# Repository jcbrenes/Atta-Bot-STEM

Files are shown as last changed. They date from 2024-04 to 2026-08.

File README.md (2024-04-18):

# Atta-Bot-STEM

Proyecto de investigación Atta-Bot STEM del Tecnológico de Costa Rica (código VIE 5402-1440-5101), con participación de la Escuela de Matemática y la Escuela de Ingeniería Mecatrónica. 

## Objetivo 
Diseñar y desarrollar una plataforma robótica de bajo costo, compuesta por un robot educativo acompañado de una aplicación computacional interactiva y amigable, guías de trabajo llamadas unidades didácticas y manuales de usuario, con el propósito de fomentar y fortalecer la enseñanza de las ciencias, tecnología, ingeniería y matemáticas (STEM) en estudiantes de Educación General Básica (EGB).

## Período de ejecución
Enero 2024 - Diciembre 2026

## Equipo investigador
- **Cindy Calderón Arce.** ORCID: https://orcid.org/0000-0002-0077-225X  
- **Rebeca Solís Ortega.** ORCID: https://orcid.org/0000-0002-3065-8386  
- **Juan Carlos Brenes Torres.** ORCID: https://orcid.org/0000-0001-6323-2173  
- **Dylana Freer Paniagua.** ORCID: https://orcid.org/0009-0005-8539-7901  

## Directorio de carpetas
- App -> Directorio con el código fuente para la aplicación de programación del robot
- Robot -> Proyecto en Arduino IDE para la programación del controlador del robot
- Chasis -> Diagramas y archivos para el chasís y parte mecánica del robot
- Materiales -> Lista de materiales usados en la construcción del robot
- Docs -> Documentos que describen el armado, programación, y uso del robot.
- Publicaciones -> Datos y materiales referentes a publicaciones del proyecto en revistas científicas.  

## Estándar de programación
Para contribuciones al proyecto se debe seguir el estándard de código o programación detallado en el archivo [Contributing.md]

[Contributing.md]: <https://github.com/jcbrenes/Atta-Bot-STEM/blob/main/CONTRIBUTING.MD>

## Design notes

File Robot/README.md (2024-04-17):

# Directorio Robot 

 Código para la programación del controlador del robot

 Lenguaje: C++
 Ambiente de programación: Arduino IDE
 Microncontrolador usado: IdeaBoard (basada en ESP32)

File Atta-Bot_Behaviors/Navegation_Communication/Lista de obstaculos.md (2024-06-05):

# Lista de mensajes

Distribución de los mensajes:
- Los mensajes se componen de 7 valores separados por ";" y el orden de lectura es:
	- ID: número de identificación del robot
	- Coordenada X
	- Coordenada Y
	- Orientación
	- Tipo de mensaje
	- Distancia a obstaculo: para sensor sharp
	- Ángulo de obstaculo: para sensor sharp

El tipo de mensaje indica a que se refiere el resto de la información en el mensaje.

Lista de tipos de mensajes que se van a recibir en la base:
- 0: Identifica posición sin obstaculo
- 1: Sharp, da medida de distancia y ángulo
- 2: IR frontal
- 3: IR derecho
- 4: IR izquierdo
- 5: Temperatura
- 6: Batería baja 
- 15: El Atta completó la función avanzarCoordenada y deja de avanzar
- 20: Medición de distancia inicial para coordinación de coordenadas
- 40: Falla de magnetómetro
- 41: Falla de MPU

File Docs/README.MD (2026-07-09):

# Documentación proyecto Atta-Bot STEM

Documentación que describe la arquitectura, protocolos, uso y programación del robot y la aplicación

ATTABUGS: https://estudianteccr-my.sharepoint.com/:x:/g/personal/prof\_ccalderon\_estudiantec\_cr/IQCo-vc9WYxwTrwLP-bhTWXTAcZCWMQx9sQ\_CMA\_rZHOI40?rtime=Aeg34Gbd3kg

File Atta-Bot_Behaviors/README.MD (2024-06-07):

**Atta-Bots: Adaptaciones, comportamientos y funcionalidades en el marco de los proyectos PROE**

Proyecto de investigación Atta-Bots del Tecnológico de Costa Rica (código VIE 5402-1440-5101), con participación de la Escuela de Matemática y la Escuela de Ingeniería Mecatrónica.

Objetivo:
Diseñar nuevos comportamientos y funcionalidades en los Atta-Bots construidos en PROE: E1F2 para disminuir la incertidumbre entre lo simulado y lo real.

Período de ejecución:
Enero 2022 - Diciembre 2023

Equipo investigador:

Cindy Calderón Arce. ORCID: https://orcid.org/0000-0002-0077-225X

Rebeca Solís Ortega. ORCID: https://orcid.org/0000-0002-3065-8386

Juan Carlos Brenes Torres. ORCID: https://orcid.org/0000-0001-6323-2173

Repositorio de: 

Código computacional de comunicación entre robots.

Código computacional de mapeo en tiempo real.

Código computacional de generación de rutas óptimas en tiempo real.

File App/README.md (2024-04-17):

# Directorio App
Código para la aplicación de programación del robot.

Lenguaje: 
Ambiente de programación:
Requerimientos:

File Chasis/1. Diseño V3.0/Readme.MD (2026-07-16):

El archivo de ensamble del Robot AttaBot completo se llama "Ensamble\_completo.iam".

Este ha sido trabajado por última vez en Inventor 2027.

Cabe destacar que existe una pieza tipo iPart que es la base del chasis. Esta contiene una tabla de parámetros para los cotas de la pieza realizado por el antiguo asistente llamado Carlos Arguello (un grande).

Sin embargo la piezas piezas "Bumper Trasero" y "Esquinero Trasero" fueron creadas a partir de esta pieza mencionada, por lo cuál inventor genera una carpeta automáticamente de cada pieza para mantener la tabla de componentes original. Es por esta razón que aislamos estas carpetas en la llamada "iParts". Por favor NO eliminar esta carpeta porque generaría problemas de reconstrucción del ensamble.

La carpeta de Set de Herramientas son todos los archivos referentes al TFG del estudiante Jose Carlos. En en ensamble Completo ya se encuentra el ensamble de Jose Carlos del Set de Herramientas incluido. Si que quisiera suprimir use como guia la imagen "GuiaParaQuitarElSetDeHerrmientasDentroDelEnsamble.png", esto sería seleccionando las carpetas del ensamble que interesan y usando la operación ISOLATE. 

La carpeta Content Center Files contiene toda la tornillería del ensamble para no depender de si el usuario tiene el instalado la carpeta de Toolbox o no. De momento hacen falta alguna que otra tuerca o tornillo en el ensamble, pero de poca relevancia para el estado actual del proyecto.

La Carpeta de "Molde para Curva Trasera" contiene todo el trabajo en inventor realizado para el molde de la curva por si quisiera rediseñar el mismo. Sin embargo el archivo pdf listo para mandar a cortar otro molde se encuentra en la carpeta de "Archivos para impresión".

Las carpetas de "OldVersions" que aparecen por todo lado son creadas automáticamente por Inventor cuando se actualizan archivos. Estarlas limpiando continuamente es una buena práctica para no llenar el git de basura, ya que el control de versiones se maneja con los commits directamente.

Redactado el 13/07/2026 por el asistente Aarón Valerín Páez (aavalerin@estudiantec.cr)

&#x20;

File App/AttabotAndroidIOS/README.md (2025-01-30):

# Atta-Bot Educativo
El proyecto Attabot Educativo es un proyecto de código abierto que busca fomentar la educación en la programación y robótica en niños y jóvenes de una manera divertida y sencilla.

**Dentro de este proyecto se encuentra el código fuente de la aplicación móvil que se conecta con el robot Attabot**

## Requisitos
- Android Studio
- Dispositivo Android con versión 5.0 o superior
- Flutter SDK
- (Opcional) Extensiones de VSCode para Flutter y Dart

## Instalación
1. Clonar el repositorio
```bash
git clone
```

2. Abrir el proyecto en VSCode 
```bash
cd Atta-Bot-STEM/App/AttabotAndroidIOS
code .
```

3. Ejecutar el proyecto
```bash
flutter run
```

## Estructura del proyecto
El proyecto utiliza una estructura basada en Screaming Architecture y componentes, la cual se divide en tres capas principales:

- **Features**: Contiene las funcionalidades de la aplicación, cada funcionalidad se divide en componentes, enums, models y services.
```
    - feature1
        - components
        - enums
        - models
        - services
    - feature2
        - components
        - enums
        - models
        - services
```

- **Pages**: Contiene las páginas de la aplicación, cada página se divide en un archivo para la página y un archivo para cada componente de la página. Dentro de cada pagina se importan las funcionalidades necesarias.
```
    - page1
        - home.dart
        - page1.dart
        - page2.dart
```

- **Shared**: Contiene los componentes servicios e interfaces compartidos entre diferentes funcionalidades, como botones, inputs, etc.

```
    - components
        - button.dart
        - input.dart
    - interfaces
        - bluetoothServiceInterface.dart
    - features
        - components
        - enums
        - models
        - services

```

## Contribuir
Para continuar contribuyendo al proyecto es necesario que el codigo este escrito en **INGLES** y seguir los siguientes pasos:

1. Crear una rama con el nombre de la nueva funcionalidad
```bash
git checkout -b feature/nombre-de-la-funcionalidad
```

2. Realizar los cambios necesarios

3. Hacer commit de los cambios con un mensaje descriptivo en ingles utilizando [Conventional Commits](https://www.conventionalcommits.org/en/v1.0.0-beta.4/)
```bash
git add .
git commit -m "feat: nueva funcionalidad" 
```

## Documentacion de referencia
Ya que el tiempo para documentar adecuadamente el proyecto fue limitado se recomienda revisar en profundidad la siguiente documentacion de referencia:

- [Flutter](https://flutter.dev/docs)
- [Dart](https://dart.dev/guides)
- [Provider](https://pub.dev/documentation/provider/latest/)
- [Flutter Blue Plus](https://pub.dev/documentation/flutter_blue_plus/latest/)

> **Nota:** Es posible que la documentacion de alguna de las dependencias no coincida con la version utilizada en este proyecto, para ello se recomienda revisar la documentacion de la version especifica en el archivo `pubspec.yaml`

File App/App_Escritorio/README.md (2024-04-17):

Aplicación de escritorio desactualizada. No cuenta con soporte o actualizaciones.

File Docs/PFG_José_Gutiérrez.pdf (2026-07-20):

Instituto Tecnológico de Costa Rica

Escuela de Ingeniería Mecatrónica

## Diseño de la expansión de la plataforma robótica Atta-Bot STEM

Informe de Proyecto de Graduación para optar por el título de

Ingeniero en Mecatrónica con el grado académico de Licenciatura

José Carlos Gutiérrez Zúñiga

Cartago, 23 de junio de 2026

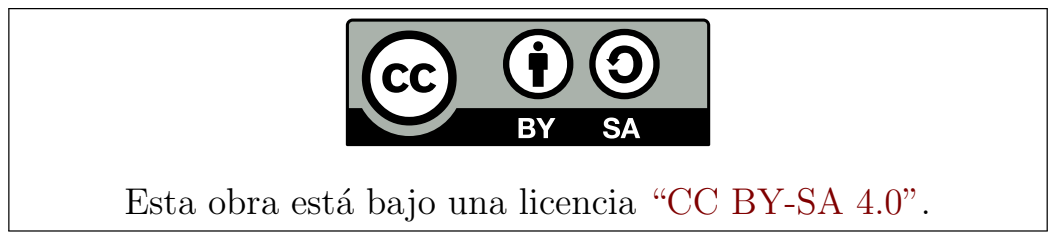
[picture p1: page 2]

Esta obra está bajo una licencia “CC BY-SA 4.0”. (https://creativecommons.org/licenses/by-sa/4.0/deed.en)

Declaro que el presente Proyecto de Graduación ha sido realizado enteramente por mi persona, utilizando y aplicando literatura referente al tema e introduciendo conocimientos propios.

En los casos en que he utilizado bibliografía, he procedido a indicar las fuentes mediante las respectivas citas bibliográficas. En consecuencia, asumo la responsabilidad total por el trabajo de graduación realizado y por el contenido del correspondiente informe final.

José Carlos Gutiérrez Zúñiga

Cartago, 23 de junio de 2026

Céd: 1-1693-0685

### INSTITUTO TECNOLÓGICO DE COSTA RICA PROGRAMA DE LICENCIATURA EN INGENIERÍA MECATRÓNICA PROYECTO FINAL DE GRADUACIÓN ACTA DE APROBACIÓN

El profesor asesor del presente trabajo final de graduación, indica que el documento presentado por el estudiante cumple con las normas establecidas por el programa de Licenciatura en Ingeniería Mecatrónica del Instituto Tecnológico de Costa Rica para ser defendido ante el jurado evaluador, como requisito final para aprobar el curso Proyecto Final de Graduación y optar así por el título de Ingeniero(a) en Mecatrónica, con el grado académico de Licenciatura.

Estudiante: José Carlos Gutiérrez Zúñiga.

Proyecto: Diseño de la expansión de la plataforma robótica Atta-Bot STEM.

### M.Sc. Johanna Vanessa Muñoz Pérez

### Asesora

### Cartago, 23 de Junio del 2026

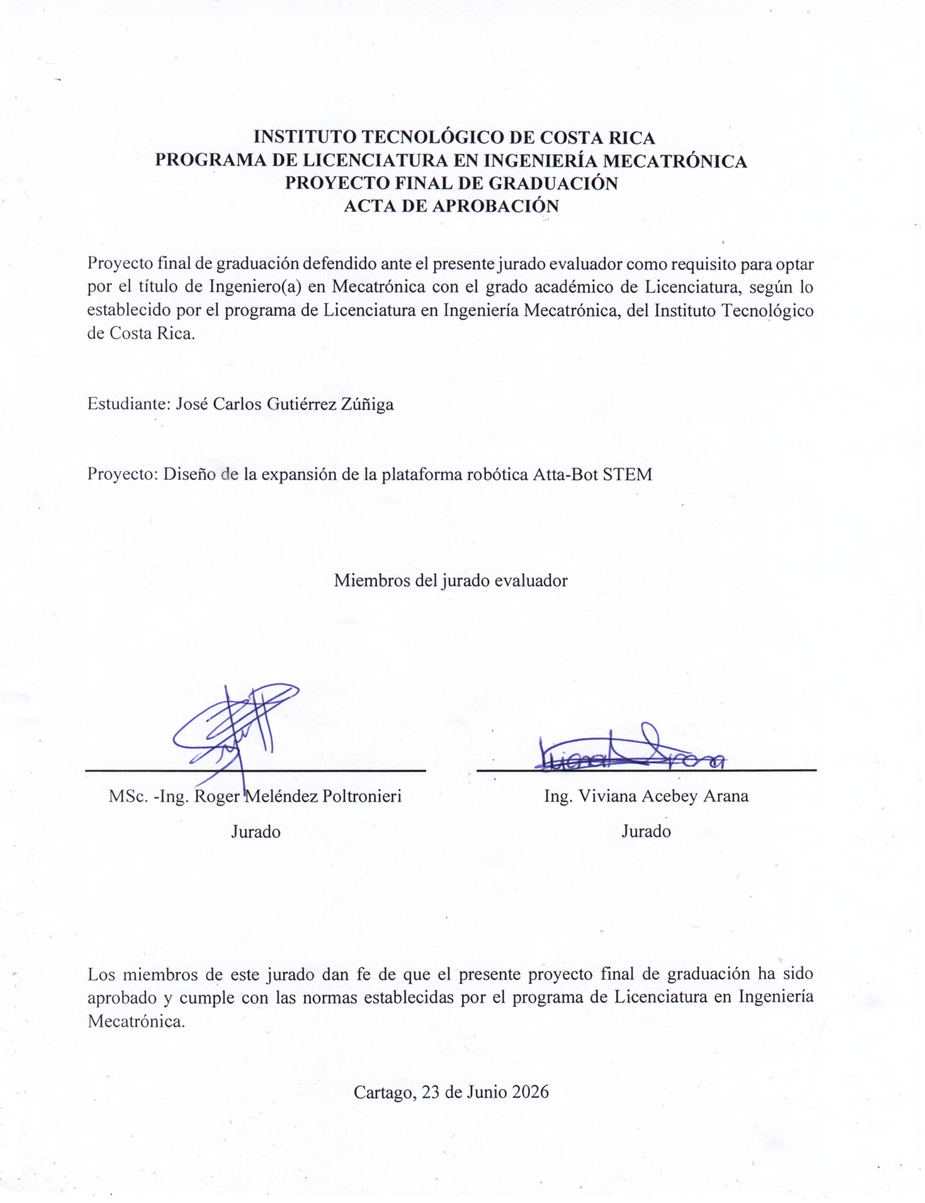
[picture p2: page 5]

# CONSTANCIA

La que suscribe, Marian Víquez Soto, Licenciada en Literatura y Lingüística con énfasis en Español y Bachiller en la Enseñanza del Español, de la Universidad Nacional.

# HACE CONSTAR

Que se ha realizado la revisión de corrección de estilo dentro de los marcos generales de redacción del informe de Proyecto Final de Graduación, modalidad tesis titulado: «Diseño de la expansión de la plataforma robótica Atta-Bot STEM» del estudiante responsable de la investigación: José Carlos Gutiérrez Zúñiga, cédula #116930685 para optar por el grado académico de Licenciatura en Ingeniería en Mecatrónica del Instituto Tecnológico de Costa Rica; la misma cumple con los requisitos exigidos en la redacción de trabajos finales de graduación.

Por lo tanto, se declara SUFICIENTE y PERTINENTE en todo su contenido.

Se extiende la presente a solicitud de los interesados, Instituto Tecnológico de Costa Rica, para los fines que consideren pertinentes y convenientes, en la ciudad de Heredia, a los doce días del mes de junio del dos mil veintiséis.

Marian Víquez Soto.

Cédula 402270133.

Carné 88995.

# Resumen

Este proyecto se enfocó en la expansión de la plataforma robótica educativa Atta-Bot STEM, desarrollada por el laboratorio GIRoM del Instituto Tecnológico de Costa Rica. El trabajo abordó tres carencias principales: la ausencia de instrucciones de bifurcación lógica, la falta de herramientas mecánicas de interacción con el ambiente y la necesidad de control desde Windows.

Para ello, se utilizó una metodología basada en Ulrich y Eppinger, que incluyó definición de necesidades, especificaciones, generación de conceptos y pruebas de validación. Como resultado se implementaron instrucciones condicionales (If y While) basadas en sensores infrarrojos en el microcontrolador, se diseñaron dos módulos de herramientas intercambiables (garra horizontal para recolección de cubos y grúa vertical para transporte de cartas) fabricadas mediante impresión 3D y corte láser y se desarrolló AttaScratch,una aplicación Web basada en el sistema de extensiones no oficiales de Scratch y con comunicación BLE para lograr el control del robot desde Windows.

Por último, se destaca que el proyecto cumplió con todas las métricas establecidas, logrando expandir las capacidades de la plataforma AttaBot-STEM mediante instrucciones de bifurcación lógicas basadas en sensores infrarrojos, empleando un set de herramientas de bajo costo apto para el uso en ambientes educativos y control multiplataforma.

Palabras clave: comunicación Web Bluetooth, extensión no oficial de Scratch, herramientas mecánicas intercambiables, robótica educativa, robótica móvil.

# Abstract

This project focused on expanding the Atta-Bot STEM educational robotics platform, developed by the GIRoM laboratory at the Technological Institute of Costa Rica. The work addressed three main shortcomings: the absence of logical branching instructions, the lack of mechanical tools for interacting with the environment, and the need for Windows-based control.

A methodology based on Ulrich and Eppinger was used, which included requirements definition, specifications, concept generation, and validation testing. As a result, conditional instructions (If and While) based on infrared sensors were implemented in the microcontroller; two modules of interchangeable tools (a horizontal gripper for collecting cubes and a vertical crane for transporting cards) were designed and manufactured using 3D printing and laser cutting, and AttaScratch was developed, an application based on the unofficial Scratch extension system with BLE communication to control the robot from Windows.

Finally, it is worth noting that the project met all established metrics, successfully expanding the capabilities of the AttaBot-STEM platform through logical branching instructions based on infrared sensors, a low-cost set of tools suitable for use in educational environments and multiplatform control.

Keywords: educational robotics, interchangeable mechanical tools, mobile robotics, unofficial Scratch extension, Web Bluetooth communication.

A mi familia, y especialmente a mamá, sin su ayuda y su apoyo, no estaría acá. Mis largas noches y viajes nocturnos, fueron sacrificio tanto mío como suyo.

# Agradecimientos

Agradezco a todos los compañeros hechos amigos con quienes compartimos proyectos, clases, estrés, trasnochadas, notas y risas. Con ustedes se formaron mis recuerdos más preciados de la universidad y fueron mi familia lejos de casa.

A todos los profesores que nos explicaban, corregían y regañaban. Gracias a su interés y dedicación, aprendimos a ser mejores estudiantes, ingenieros y hasta personas.

Al laboratorio GIRoM, por la guía y la aceptación del proyecto, así como por la ayuda que cada uno de sus integrantes aportó durante el desarrollo de este trabajo de graduación.

Por último, a esas personitas especiales cuyo cariño y apoyo me sostuvieron en los momentos difíciles, que me ayudaron a sostener y aliviar las cargas del proyecto, la carrera y la vida.

Este proyecto fue posible gracias al aporte de todos y cada uno de ustedes.

¡Muchas gracias a todos!

José Carlos Gutiérrez Zúñiga

Cartago, 23 de junio de 2026

´

# Indice general

Lista de figuras | v
Lista de tablas | vii
Lista de abreviaciones | ix
1 Introducción | 1
2 Marco Teórico | 5
3 Metodología | 13

i

ii | Índice general
3.3.1 | Definición de métricas, valores ideales y marginales de las especifica-
ciones enfocadas en la programación del microcontrolador del robot . | 17
3.3.2 | Definición de métricas, valores ideales y marginales de las especifica-
3.3.3 | Definición de métricas, valores ideales y marginales de las especifica-
ciones enfocadas en la plataforma de control de robot desde Windows | 23
3.5.2 | Funcionalidad de la expansión lógica de condicionales con base en los
4 Desarrollo de la expansión del AttaBot-STEM | 41
4.3 Desarrollo de la solución de la plataforma de control desde Windows | . . . . | 57

4.4 Desarrollo de la solución de la modificación de la programación del microcon-

5 Resultados y Análisis | 73
5.1.2 | Funcionalidad de la expansión lógica de condicionales con base en los

Índice general | | iii
5.1.8 | Intercompatibilidad entre plataformas | | 87
5.1.9 | Resumen de los resultados | | 88
5.2 Análisis Económico | | 89
5.2.1 | Investigación y desarrollo | | 89
5.2.2 | Módulo de motor | | 90
5.2.3 | Módulo de la garra | | 90
5.2.4 | Módulo de la grúa | | 91
5.2.5 | Desarrollo de software | | 91
5.2.6 | Resumen de costos | | 92
5.2.7 | Beneficios | | 92
6 Conclusiones y Recomendaciones | 95
6.1 Conclusiones | | 95
6.2 Recomendaciones | | 95
A Código del microcontrolador | 103
B Código AttaScratch | 105
C Proyecto plantilla tutorial de AttaScratch | 107
D Videos evidencia de la validación | 109
E Planos Mecánicos | 111

iv | Índice general

´

# Indice de figuras

2.1 Fotografías del AttaBot-STEM | | 6
2.2 Interfaz de usuario de Atta-Bot aplicación | | 8
2.3 Imagen de la tienda del TruetrueBot | | 9
2.4 Foto de redes sociales del Titibot | | 10
2.5 Fotografía de noticias de RobIE++ | | 10
3.1 Diagrama funcional de caja negra de la modificación al código del robot | . . | 26
3.2 Diagrama funcional de caja negra del set de herramientas | | 26
3.3 Diagrama funcional de caja negra de la aplicación de control desde Windows | 27
3.4 Diagrama funcional de subproblemas de la modificación de la programación
del microcontrolador del robot | | | 27
3.5 Diagrama funcional de subproblemas del set de herramientas | | | 28
3.6 Diagrama funcional de subproblemas de la plataforma de control desde Win-
dows | | 29
4.1 Diagrama del proceso de solución propuesto | | 42
4.2 Foto del ensamble de la base del motor | | 43
4.3 Acoplador del eje al motor | | 44
4.4 Eje del motor | | 44
4.5 Soporte del eje del motor | | 45
4.6 Soportes en L | | 45
4.7 Base del motor | | 46
4.8 Base del motor | | 46
4.9 Mecanismo de garra para el Attabot-STEM | | 47
4.10 Engranes Biselados | | 48
4.11 Eje del mecanismo de transmisión de los engranes | | 48
4.12 Ejes del mecanismo de transmisión de las pinzas | | 49
4.13 Soporte de eje | | 50
4.14 Pinzas de la garra | | 51
4.15 Acoplador entre eje de potencia y del mecanismo | | 51
4.16 Retenedores del mecanismo | | 52
4.17 Bases general de ensamble | | 52
4.18 Bases estructurales del ensamble | | 53
4.19 Mecanismo de grúa para el Attabot-STEM | | 54
4.20 Eje de transmisión al mecanismo de grúa | | | 54

v

vi | Índice de figuras
4.21 Eje de enrollado de cuerda | | 55
4.22 Eje de soporte de la carga | | 55
4.23 Elemento pesa | | 56
4.24 Paredes laterales | | 56
4.25 Bloque Avanzar | | 58
4.26 Bloque Retroceder | | 58
4.27 Bloque Girar izquierda | | 58
4.28 Bloque Girar derecha | | 59
4.29 Bloque For | | 59
4.30 Bloque Detección iniciada de obstáculos | | 60
4.31 Bloque Detección finalizada de obstáculos | | 60
4.32 Bloque Activar Lápiz | | 60
4.33 Bloque Desactivar Lápiz | | 61
4.34 Bloques Configuración de Lápiz | | 62
4.35 Bloque If | | 63
4.36 Bloque If Else | | 64
4.37 Bloque If ElseIf | | 64
4.38 Bloque If ElseIf Else | | 64
4.39 Bloque While | | 65
4.40 Bloque While not | | 65
4.41 Bloque Herramienta | | 66
4.42 Bloque Mensaje de comandos | | 66
4.43 Bloque Envío BLE | | 67
4.44 Bloque Reconectar | | 67
4.45 Bloque Modo transmisión BLE | | 67
4.46 Bloque Exportar | | 68
4.47 Bloque de importar de .dat | | 68
4.48 Diagrama de la máquina de estados propuesta | | 69
5.1 Comandos actuales | | 74
5.2 Caja de guardado de sets | | 78
5.3 Simulación de algoritmos en Scratch | | 86
A.1 Captura del repositorio del código del microcontrolador del robot | 103
B.1 Captura del repositorio de AttaScratch | 105
C.1 Captura de AttaScratch | 107
D.1 Directorio de OneDrive con videos de las pruebas | 109
D.2 Directorio de Mega con videos de las pruebas | 110

´

# Indice de tablas

3.1 Tabla de importancia relativa de las necesidades críticas | | 15
3.2 Tabla de importancia relativa de las necesidades deseadas | | 16
3.3 Tabla de importancia relativa de las necesidades aceptables | | 16
3.4 Métricas propuestas para las necesidades enfocadas en la programación del
microcontrolador del robot | 17
3.5 Matriz de correspondencia entre necesidades y métricas de enfocadas en la
programación del microcontrolador del robot | | 18
3.6 Métricas propuestas para las necesidades enfocadas en el hardware del robot | 19
3.7 Matriz de correspondencia entre necesidades y métricas de enfocadas en el
hardware del robot | 20
3.8 Métricas propuestas para las necesidades enfocadas en la plataforma de control
de robot desde Windows | 23
3.9 Matriz de correspondencia entre necesidades y métricas enfocadas en la plataforma
de control de robot desde Windows | | 24
3.10 Filtrado de los conceptos para el subproblema de Fuente eléctrica | | 31
3.11 Selección de los conceptos para el subproblema de la Fuente eléctrica . . . . | 32
3.12 Filtrado de los conceptos para el subproblema de Convertir a rotación mecánica 33 3.13 Selección de los conceptos para el subproblema de Convertir a rotación mecánica 34
3.14 Filtrado de los conceptos para el subproblema del Accionar de Herramientas | 35
3.15 Selección de los conceptos para el subproblema de Accionar de Herramientas | 36
3.16 Asociación entre pruebas y las métricas a las que responden | | 38
5.1 Tabla de registros de las pruebas de validación de compatibilidad actual . . . | 75
5.2 Registro de los ensayos de la prueba de validación de funcionalidad de la
expansión lógica de condicionales con base en los sensores infrarrojos . . . . | 75
5.3 Resumen de características varias para la aptitud del uso escolar | | 78
5.4 Resumen de acciones de ensamble de Garra | | 79
5.5 Resumen de acciones de ensamble de Grúa | | 79
5.6 Resumen de acciones de ensamble de Base del Motor | | 79
5.7 Resumen de acciones para el intercambio de herramientas | | 79
5.8 Resumen de las características del diseño del set de herramientas, en com-
paración con la guía de edades | 80
5.9 Resumen de los ensayos de resistencia por caídas del set de herramientas.
(Primeros 15 ensayos con la garra, el resto con la grúa) | 80

vii

viii | Índice de tablas

5.10 Resultado de los ensayos de validación de estabilidad por el centro de masa
de la garra | 83
5.11 Resultado de los ensayos de validación de estabilidad por el centro de masa
de la grúa | | 84
5.12 Resultados de los ensayos de validación de los comandos de las herramientas | 85
5.13 Resultado de los ensayos de validación de la simulación de los comandos en
Scratch | 86
5.14 Registro de las pruebas de validación de la transmisión de comandos desde
Scratch | 87
5.15 Resumen de los ensayos de validación del Importar/Exportar archivos de
guardado de la aplicación Android | | 87
5.16 Resumen del cumplimiento de las métricas | | 88
5.17 Costos directos de investigación y desarrollo | | 89
5.18 Costos indirectos de investigación y desarrollo | | 90
5.19 Costos directos del módulo del motor | | 90
5.20 Costos directos del módulo de la garra | | 90
5.21 Costos directos del módulo de la grúa | | 91
5.22 Costos directos del desarrollo del software | | 91
5.23 Costos indirectos del desarrollo de Software | | 92
5.24 Resumen de costos | | 92

# Lista de abreviaciones

### Abreviaciones

API | Interfaz de Programación de Aplicaciones (por sus siglas en inglés)
BLE | Bluetooth Low Energy
CAD | Diseño Asistido por Computadora (por sus siglas en inglés)
CD | Corriente Directa
CPSC | Comisión de Seguridad de Productos del Consumidor de Estados Unidos
FM | Frecuencia Modulada
GATT | Perfil de Atributo Genérico (por sus siglas en inglés)
GIRoM | Grupo de Investigación en Robótica Múltiple
IDE | Entorno de Desarrollo Integrado (por sus siglas en inglés)
JSON | JavaScript Object Notation
LED | Diodo Emisor de Luz (por sus siglas en inglés)
MEP | Ministerio de Educación Pública
OS | Sistema Operativo (por sus siglas en inglés)
PETG | Polietileno tereftalato glicol (por sus siglas en inglés)
PID | Proporcional Integral Derivativo
PLA | Acido poliláctico (por sus siglas en inglés) ´
PROE | Planificación de Rutas Optimas por Enjambres ´
PWM | Modulación por Ancho de Pulso (por sus siglas en inglés)
STEM | Ciencia, Tecnología, Ingeniería y Matemática (Por sus siglas en ingles)
TPU | Poliuretano Termoplástico (por sus siglas en inglés)
UUIDs | Identificador Unico Universal (por sus siglas en inglés) ´

ix

x | Lista de abreviaciones

# Capítulo 1

# Introducción

## 1.1 Contexto

El proyecto PROE (Planificación de Rutas Optimas por Enjambres) es un proyecto de investi- ´

gación del Instituto Tecnológico de Costa Rica en el que colaboran la Escuela de Matemática y la Escuela de Ingeniería Mecatrónica, iniciado en 2019, con el objetivo de diseñar un sistema multirobot físico para la exploración y digitalización de escenarios y determinación de rutas óptimas [1].

Dentro de este proyecto se diseñó un robot llamado Atta-Bot, el cual es utilizado en modo de enjambre, al emplear simultáneamente múltiples de estos Atta-Bots [2]. Posteriormente, con base en el proyecto PROE, el laboratorio desarrolló un nuevo proyecto llamado Atta Bot-STEM [3]; es en este proyecto del grupo de investigación que el presente proyecto de graduación tiene lugar.

Este proyecto de investigación Atta-Bot STEM del Tecnológico de Costa Rica (código VIE 5402-1440-5101), con participación de la Escuela de Matemática y la Escuela de Ingeniería Mecatrónica, busca diseñar y elaborar una plataforma robótica desarrollada por el TEC, de bajo costo, compuesta por un robot educativo, acompañado de una aplicación computacional interactiva y amigable, así como de guías de trabajo llamadas “unidades didácticas” y “manuales de usuario”, con el propósito de fomentar y fortalecer la enseñanza de las ciencias, tecnología, ingeniería y matemáticas (STEM) en estudiantes de Educación General Básica (EGB). [4]

1

2 1.2 Problema

## 1.2 Problema

En sí mismo, el proyecto de investigación Atta Bot-STEM, responde a la necesidad del desarrollo y mejora de la educación pública en el país. Esto lo realiza mediante una plataforma robótica abierta y de bajo costo, software interactivo y de control de código abierto, así como de guías de trabajo para el uso del robot en las aulas. Actualmente, el proyecto Atta-Bot STEM se encuentra en proceso de desarrollo para cumplir sus objetivos. Por lo que, por el momento la plataforma robótica cuenta con un set de instrucciones limitado (desplazamientos, rotaciones, un ciclo), un marcador como única interacción externa y un control por medio de una aplicación Android.

A partir de lo anterior, en este proyecto se busca continuar con el desarrollo de la plataforma Atta Bot-STEM, aumentando su valor con mayores capacidades de interacción física en el aula, su set de instrucciones y de la plataforma de control.

### 1.2.1 Síntesis del problema

Pese al desarrollo previo en el proyecto AttaBot-STEM, se tienen las carencias de no contar con instrucciones de bifurcación lógica, herramientas mecánicas de interacción con el ambiente y control desde la plataforma Windows. Por lo tanto, se requiere el diseño de soluciones a estas carencias.

## 1.3 Objetivos

### 1.3.1 Objetivo General

Potenciar la propuesta de valor de la plataforma robótica Atta Bot-STEM para las instituciones educativas mediante la implementación de herramientas mecánicas, instrucciones de bifurcación lógicas y control del robot desde Windows.

### 1.3.2 Objetivos Específicos

1. Diagnosticar los requerimientos tecnológicos para las modificaciones a la plataforma Atta Bot-STEM.
2. Programar la simulación de los algoritmos y el control del robot desde Windows.
3. Programar comportamientos if y while con la capacidad de lecturas de sensores presentes en la arquitectura implementada en el microcontrolador.
4. Construir un kit de herramientas mecánicas para actividades pedagógicas en las aulas.
5. Validar la funcionalidad de los sistemas implementados mediante pruebas funcionales.

1 Introducción | 3

## 1.4 Estructura del documento

- Capítulo 1. Introducción ≫ Se encuentra la descripción de la problemática con-

textual y de objetivos del proyecto.

- Capítulo 2. Marco teórico ≫ Se encuentra información de referencia del contexto,

estado del arte y científicos para el desarrollo del proyecto.

- Capítulo 3. Metodología ≫ Se encuentra el desarrollo ordenado del proceso de

diseño utilizado en el proyecto.

- Capítulo 4. Propuesta de diseño ≫ Se detallan las características del concepto

ganador y desarrollo del prototipo.

- Capítulo 5. Resultados y análisis ≫ Se presentan los resultados de las pruebas de

validación realizadas al prototipo, así como un análisis de su comportamiento.

- Capitulo 6. Conclusiones y recomendaciones ≫ Se presentan las principales

conclusiones obtenidas del desarrollo del proyecto, así como las recomendaciones de mejora o pasos futuros.

## 1.5 Aporte ingenieril

El principal aporte de la ingeniería presentado en el proyecto es la sistematización ordenada del proceso de diagnóstico e identificación de problemáticas o necesidades raíz, enfocado en un desarrollo de propuesta-solución ordenado y dirigido a ser verificado y validado de manera clara.

4 1.5 Aporte ingenieril

# Capítulo 2

# Marco Teórico

## 2.1 Plataforma AttaBot-STEM

El proyecto actual se basa en la plataforma existente AttaBot-STEM (fig.2.1) desarrollada por el laboratorio GIRoM para ser utilizada en ambientes educativos. La primera iteración del diseño del AttaBot-STEM se realizó en el 2024 [3], donde se buscó abaratar y simplificar el diseño de los robots enjambre de exploración del laboratorio GIRoM llamados AttaBot [2]. Para ello, se realizó un rediseño, en función de las necesidades del uso del robot en la educación [3].

De este proceso de rediseño se destaca:

- Cambio del sistema de doble microcontrolador a una sola tarjeta IDEABOARD [5]

para el control de actuadores, sensores, instrucciones y comunicación.

- Cambio de comunicación de Radio FM a BLE.
- Cambio de sensores de posicionamiento y exploración complejos, por rutinas simples

de evasión, a partir de sensores infrarrojos.

- Cambio de enfoque del ensamble de uniones permanentes a un enfoque modular que permita el arme/desarme, así como el reemplazo fácil de piezas.
- Inclusión en el diseño de sensores y actuadores para realizar actividades educativas en

las aulas.

- Inclusión de un método simple de “programación” de instrucciones y acciones al robot desde una aplicación móvil mediante comandos de 5 caracteres [6].
- Diseño e implementación de la máquina de estados [7] que lee y ejecuta comandos

transmitidos por BLE, así como el estándar de decodificación de instrucciones.

En el segundo semestre del 2024, se da la segunda iteración del proceso de rediseño del AttaBot-STEM, la cual se enfocó en mejorar la robustez mecánica, la protección de los

5

6 2.1 Plataforma AttaBot-STEM

componentes electrónicos, la distribución de peso, el diseño del sistema de control PID de los motores y la implementación de un primer actuador en un sostenedor de marcadores en el centro del robot para marcar su trayectoria [8].

Durante el 2025, el trabajo en la plataforma se mantuvo enfocado en calibración, estética y aspectos pedagógicos. El cambio destacable para el proyecto actual es la eliminación de una botonera que liberó pines del IDEABOARD para ser utilizados en otras funciones.

De manera paralela al aspecto robótico, se llevó a cabo el desarrollo de una aplicación Android para el control del robot y simulación de secuencias de movimiento [9].

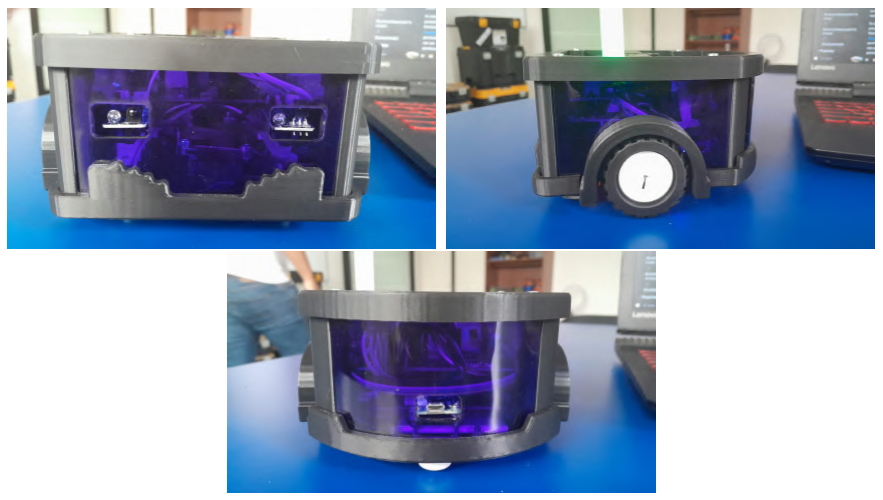
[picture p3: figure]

Figura 2.1: Fotografías del AttaBot-STEM

### 2.1.1 Ideaboard

La tarjeta del Ideaboard se basa en el chip ESP32-WROOM-32E. En el proyecto, su programación se trabaja en el IDE de Arduino con el módulo de ESP32. La tarjeta, aunque es de lógica 3.3V, cuenta con alimentación directa de 5-9VDC para la alimentación de drivers integrados y la posibilidad de alimentar pines VCC con la alimentación directa. Los pines de uso general se encuentran en configuración de cuatro pines en línea para el uso de cables del estilo de las interfaces STEMMA/QWIIC de cuatro pines. [5]

### 2.1.2 Módulo de booster

El diseño del AttaBot-STEM utiliza el módulo ”PowerBoost 1000 Charger-Rechargeable 5V Lipo USB Boost @ 1A - 1000C” (PowerBoost ADA2465) para aumentar la tensión de salida de la batería LIPO de 3.7V a 5V y para recargar la batería mediante conexión USB [10].

2 Marco Teórico | 7

### 2.1.3 Sensores infrarrojos

Los sensores infrarrojos inferiores del AttaBot-STEM son del módulo ”KY-0333 Line Tracking Sensor”. Este módulo funciona en lógica 3.3V y 5V. Emite una señal en alto al detectar baja reflectividad (superficie negra) y en bajo, al detectar alta reflectividad (superficie blanca). Finalmente, posee un potenciómetro integrado para ajustar su sensibilidad [11].

### 2.1.4 Chasis

La plataforma AttaBot-STEM al ser de bajo costo, alta disponibilidad y reemplazabilidad, el laboratorio busca que las piezas con las que se manufactura sean del menor costo posible, lo que lleva a comprar componentes estándares genéricos, open source o fabricados internamente en los laboratorios institucionales [12].

Entre los materiales y procesos con los que se está fabricando el chasis, se incluye el corte láser de láminas de acrílico de 3mm e impresión 3D con disponibilidad de PLA, TEPG y FLEX (TPU). Cabe destacar las principales propiedades de estos materiales para su uso.

Las láminas de acrílico permiten crear bases y componentes estables, rígidos y precisas, pero con geometrías limitadas. Por su parte, la impresión 3D permite geometrías más complejas, pero con limitantes mecánicas según el material. El filamento PLA es comparativamente el más rígido y teóricamente, el menos resistente. El Filamento PETG en teoría rígido y más resistente a los impactos y deformación, pero es más difícil de trabajar, por lo que, se ve limitado en el equipo de impresión que lo puede trabajar. Por último, el FLEX (TPU) es extremadamente más resistente a impactos y deformación, al ser un material flexible, es excelente en elementos de disipación de impactos, que requieran ser deformados en su uso de ajuste a presión, pero requiere equipo más especializado para ser trabajado. [13]

### 2.1.5 Atta-Bot aplicación

La Atta-Bot aplicación es un android desarrollado de manera paralela con el robot. Actualmente, incluye una interfaz de usuario amigable en la que se permite programar secuencias mediante instrucciones en bloque, guardar/cargar secuencias, observar una simulación de la secuencia y transmitir la secuencia al robot mediante BLE. La interfaz de usuario se observa en la fig.2.2.

8 2.1 Plataforma AttaBot-STEM

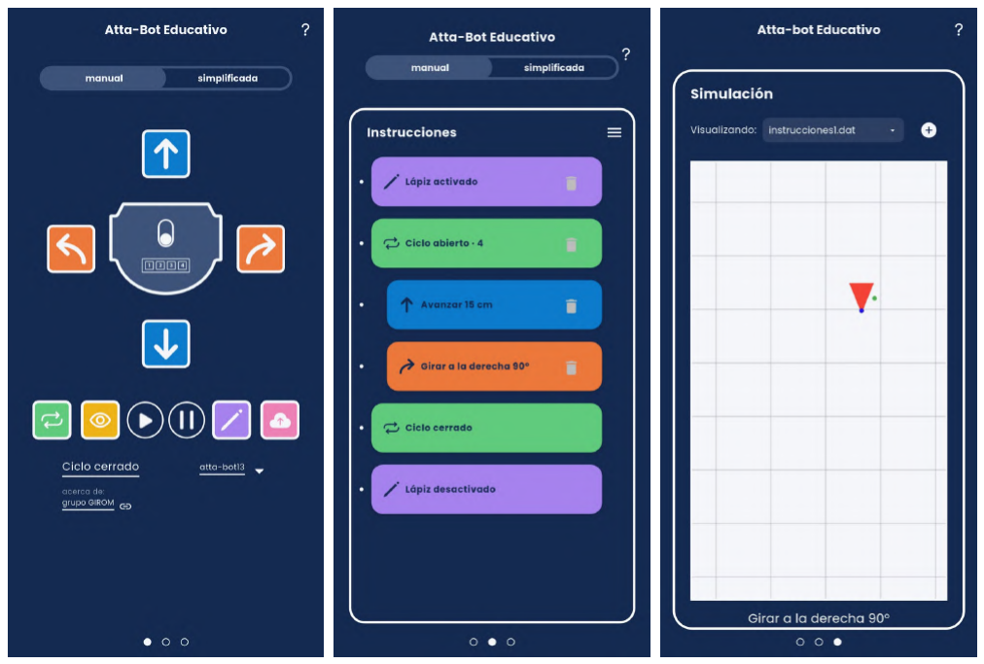
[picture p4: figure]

Figura 2.2: Interfaz de usuario de Atta-Bot aplicación

### 2.1.6 Estructura de control

La estructura de control o “programación” de las instrucciones al AttaBot-STEM es similar a la estructura de ensamblador, donde se tienen símbolos continuos que se decodifican por bloques de largo constante y donde se codifica la primera parte de la instrucción por tipo (como un OPCODE) y se indica información extra en la segunda parte (como un inmediato).

Específicamente, para el AttaBot-STEM, las instrucciones se empacan en un string de hasta 512 caracteres alfanuméricos.[14]. Cada comando es conformado por cinco caracteres. En estos cinco caracteres, el carácter 1 y 2 proporciona la información de que tipo de instrucción es (como un OPCODE de moverse) y en los caracteres 3, 4 y 5; proporciona el valor de la instrucción (similar a un inmediato, el cuanto moverse). También comandos de control (como el inicio y final) que utilizan los cinco caracteres para ser identificados, ya que no incluyen información adicional más que su marca.

Al recibir un mensaje, el robot procede a decodificar el mensaje y guardar en una matriz 100x2 los shorts identificadores de cada instrucción respectivos a cada comando en la primera fila y en la segunda fila el valor codificado de la segunda parte del comando.

Con las instrucciones y valores extraídos del string de comando, el robot avanza en su máquina de estado, ejecutando una por una las instrucciones según los valores de manera secuencial.

2 Marco Teórico | 9

## 2.2 Otras plataformas en el mercado

### 2.2.1 TrueTrueBot

El Truetruebot (fig. 2.3) es un robot educativo para niños que incluye la opción de indicarle comandos mediante cartas con codificaciones de color, acelerómetros, sensores de color para seguimientos de lineas, programación por bloques y aplicación Android. [15].

Por su parte, la plataforma Scratch de TrueTrueBot [16] es inspiración, referencia y prueba de concepto para la aplicación Windows del AttaBot-STEM. Es una instancia personalizada y con una extensión no official de Scratch que permite simular y controlar el TruetrueBot. Además, integra Web Bluetooth en el cliente de Scratch para enviar los comandos al robot.

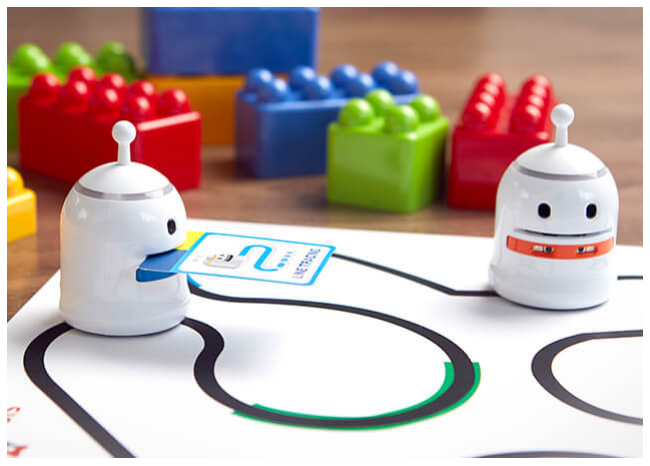
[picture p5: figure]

Figura 2.3: Imagen de la tienda del TruetrueBot

### 2.2.2 Titibots

La plataforma Titibots (fig. 2.4) y Titibots Colab fueron desarrollados por la Dra. Kryscia Ramírez para niños de 4 a 6 años en un proyecto de la UCR [17] [18] y distribuidos por RainforestLab [19] [20] . El robot diseñado a semejanza de un mono permite instrucciones de movimiento, rotación y mover sus brazos (un efector de garra) mediante una aplicación Android y comunicación Bluetooth.

10 2.3 Scratch

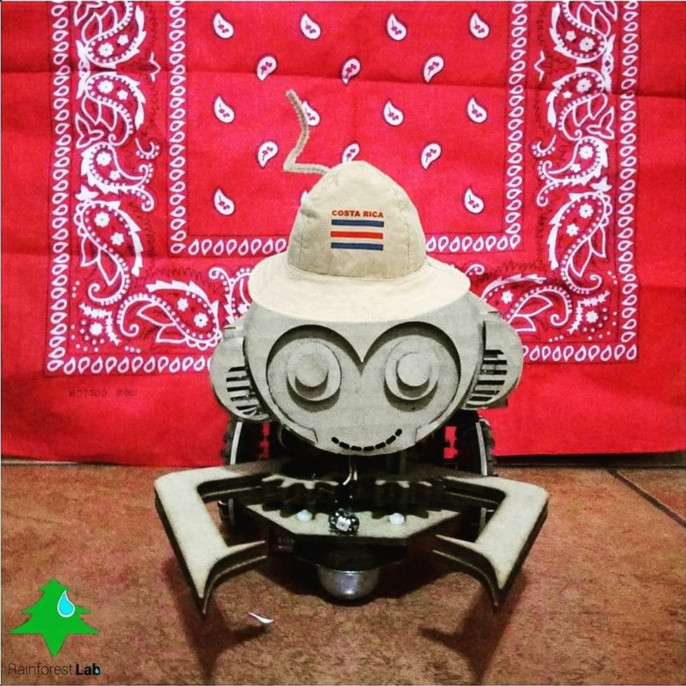
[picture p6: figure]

Figura 2.4: Foto de redes sociales del Titibot

### 2.2.3 RobIE++

Basado en los Titibots, la Fundación Omar Dengo desarrolló y distribuyó en escuelas públicas los robots RobIE++ (fig. 2.5), los cuales utilizan la aplicación Android desarrollada para los Titibots. Por lo que, este robot cuenta con instrucciones de movimiento para avanzar, retroceder, rotar, abrir y cerrar un efector simple de garra [21].

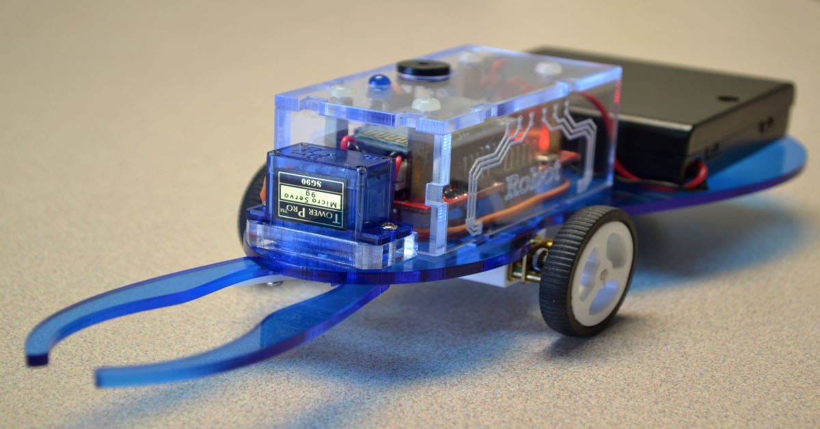
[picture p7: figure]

Figura 2.5: Fotografía de noticias de RobIE++

## 2.3 Scratch

Scratch [22] es una plataforma de código abierto de programación por bloques utilizada por el Ministerio de Educación Pública de Costa Rica (MEP) en escuelas y colegios [23]. Su pertinencia al proyecto radica en las extensiones que se pueden desarrollar para expandir sus capacidades, entre ellas las desarrolladas con LEGO de MINDSTORM EV3 [24], WeDo

2 Marco Teórico | 11

2.0 [25] y BOOST [26]. Estos sets de LEGO forman parte de los equipos que se utilizan en clases y eventos de robótica por parte del MEP [27].

Como parte de las extensiones para controlar estos equipos mencionados mediante Bluetooth se desarrolló Scratch Link [28], el cual se encarga de realizar la comunicación Bluetooth con los dispositivos. En síntesis, Scratch Link es un instancia de un navegador ejecutando una mímica de Web Bluetooth [29].

### 2.3.1 Scratch Unofficial Extensions

Scratch como proyecto de código abierto proporciona documentación para el desarrollo de sus extensiones; sin embargo, toda extensión desarrollada fuera del proyecto principal de la plataforma o sus colaboraciones (como con LEGO) es considerada una ”Unofficial Extension” (extensión no oficial). Por lo que, instancias de Scratch con extensiones no oficiales por defecto cuentan con limitaciones de acceso a ciertas propiedades internas de Scratch e interacción con las cuentas en línea de la fundación [30].

Por otra parte, las extensiones no oficiales poseen la libertad y capacitad de ejecutar cualquier proceso soportado por JavaScript, Web APIs y el navegador dentro del ambiente de programación por bloques de Scratch [31].

## 2.4 Web Bluetooth

Web Bluetooth es una API desarrollada con el objetivo de darle capacidades de comunicación Bluetooth a sitios web directamente desde el navegador de forma segura [32]. Su estado es considerado como experimental y no esta soportada en su totalidad por todos los navegadores; sin embargo, los navegadores basados en chromium soportan la mayoría de la API [33].

## 2.5 Bluetooth Low Energy (BLE)

Bluetooth Low Energy es la tecnología que el AttaBot-STEM utiliza para recibir los comandos de control. BLE limita las velocidades de transmisión de datos y mantiene el transmisor apagado la mayoría del tiempo para ahorrar energía [32]. Se utiliza el estándar del Generic Attibute Profile (GATT) para ordenar, identificar e interactuar con el sistema de servicios y características mediante números de 128bits conocidos como Universally Unique Identifiers (UUIDs) [34].

12 2.6 Tamaño de muestra

## 2.6 Tamaño de muestra

Para el proceso de validación se utilizan pruebas con resultados categorizados como éxitos y fracasos, por lo que, se utiliza la distribución binomial como referencia en el análisis [35].

Se utiliza la aproximación a distribución normal para calcular los tamaños de muestra de las pruebas mediante la ecuación 2.1

n = Z

2
- p ·

1 − p
M²

(2.1)

Donde:

- n: es el tamaño de muestra requerida.
- Z: el nivel de confianza.
- p: estimación inicial de la proporción.
- M: el margen de error o intervalo de confianza.

Al trabajar con un nivel de confianza al 90%, un margen de error del 10% y de manera conservadora, una estimación inicial de la proporción del 50% en la calculadora de muestras se obtiene un tamaño de muestra de 68 ensayos. Sin embargo, el diseño esta creado para que el sistema pase las pruebas con casi una totalidad de éxitos, por lo que, se esperaría que no falle la mitad de los ensayos.

Los sistemas programados y lógicos una vez completados, no se espera que fallen mientras el hardware y OS funcionen apropiadamente, por lo que, una estimación más realista de la proporción inicial es del 99%, lo cual resulta en un tamaño de muestra de 3 ensayos. De manera similar, los elementos mecánicos se espera que pasen las pruebas con un 90% de éxitos, lo cual resulta en un tamaño de muestra de 24 ensayos. [36]. Para darle más robustez a los datos, se decide tomar 5 y 30 muestras para cada clase respectiva de prueba.

# Capítulo 3

# Metodología

## 3.1 Resumen metodológico

Para el desarrollo del proyecto se utiliza una metodología basada en la metodología de Ulrich y Eppinger en su libro Diseño y desarrollo de productos adaptada a las necesidades de este proyecto en específico. [37].

Como primer paso para el desarrollo del proyecto se definen los sistemas a diseñar mediante listas de requerimientos del cliente en este caso, los investigadores del proyecto Atta-Bot STEM, así como una descripción detallada de la función del producto final y sus características necesarias.

Como segundo paso se tiene la recopilación de información relevante de tecnologías o estado del arte para los sistemas a diseñar. La búsqueda y análisis de información responde a la necesidad de comprender las formas o alternativas para solventar los requisitos del cliente. Para el proyecto Atta-Bot STEM se incluye investigación sobre robótica educativa, análisis de las necesidades curriculares en áreas STEM y revisión de tecnologías existentes en el ámbito educativo.

Como tercera etapa se plantean posibles soluciones a los requerimientos del cliente. Esto implica un síntesis de ideas nuevas, herramientas y métodos para llegar a una posible solución. La exploración de tecnologías es crucial en este proceso y es importante tener una visión completa del problema para plantear diversas soluciones. En el caso del Atta-Bot STEM, esto puede incluir el uso soluciones disponibles en el mercado o el diseño de elementos nuevos de hardware y software para lograr las funcionalidades del robot y su software acompañante, asegurando el cumplimiento de los requisitos del cliente.

Como cuarta etapa se realiza un estudio comparativo exhaustivo de los sistemas propuestos y se verifica cuál se alinea mejor con las especificaciones del proyecto Atta-Bot STEM. En

13

14 3.2 Definición de necesidades

esta fase se aplican conocimientos ingenieriles y los requisitos del cliente para decidir cuáles son los sistemas más viales y valiosos para el proyecto. Un método para formalizar esta decisión es mediante matrices de decisión. En estas se implementa una escala y se asigna una puntuación a cada atributo deseable en el sistema diseñado. Por lo que, basándose en estos factores y en las puntuaciones asignadas a cada concepto solución, se obtiene una nota final que valida la selección.

Como quinta fase corresponde la implementación de la solución mediante simulaciones, pruebas de concepto, un prototipo del diseño funcional o una combinación de estas para su verificación de cumplimiento de requisitos. En el caso de este proyecto se espera un prototipo de los sistemas diseñados integrados con el Atta Bot-STEM y su software acompañante.

Finalmente, de la naturaleza iterativa del proceso, los resultados de cualquiera de las etapas pueden llevar a mejoras, cambios o ajustes de las etapas anteriores para una reiteración del proceso de ser necesario.

## 3.2 Definición de necesidades

Para determinar las necesidades de la plataforma AttaBot-STEM se realizaron visitas al laboratorio GIRoM para observar la plataforma en uso y entrevistar a los asistentes sobre las capacidades y limitaciones de la plataforma. Luego, se realizaron reuniones con los profesores investigadores para aclarar los objetivos que tienen para la plataforma, así como ciertas limitaciones y requerimientos de diseño y por último, se realizó una investigación de la documentación técnica, de referencia y diseño de la plataforma para determinar los requisitos que han sido parte del proceso de desarrollo previo.

Del proceso previo se obtienen necesidades que dada su naturaleza, se considera conveniente separarlas en tres categorías: aquellas de la programación del robot mismo, aquellas del hardware del robot y aquellas del sistema de control del robot.

Además, se presentaron estas necesidades al equipo investigador para obtener su valoración sobre su importancia relativa y para identificar cualquier otra consideración que pudiera haberse pasado por alto durante el periodo inicial de entrevistas y reuniones. Para ello, se realizó la encuesta utilizando la siguiente escala de valoración:

1) La característica es indeseable. (Con esto, ya no lo quiero)
2) La característica no es importante. (Ni suma ni resta)
3) La característica es buena, pero no necesaria. (Sería lindo, pero no lo veo importante)
4) La característica es muy deseable, pero no crítica. (Me encantaría, pero podemos vivir sin ella)
5) La característica es crítica. (Sin esto, no me interesa)

Con base en las respuestas promediadas de la encuesta se presentan las necesidades agrupadas

3 Metodología | 15

en tres grupos: Críticas (5.0-4.5) en la tabla 3.1, Deseables (4.5-3.5) en la tabla 3.2 y Aceptables (3.5-2.5) en la tabla 3.3. Se aclara que en el proceso de encuesta, ninguna necesidad se evaluó con 2 o 1.

Tabla 3.1: Tabla de importancia relativa de las necesidades críticas

Número | Necesidad | Importancia Relativa
| Programación del microcontrolador
1 | Que no se interfiera el funcionamiento actual | 5,0
3 | Que se utilice el estándar de programación del proyecto descrita en Github | 4,7

Set de herramientas
8 | Que el set sea de fácil ensamblaje | 5,0
11 | Que no requiera desarme del robot | 5,0
12 | Que sea resistente para el ambiente de manipulación en el aula por niños y adolescentes | 5,0
13 | Que el diseño sea seguro para el ambiente de manipulación en el aula por niños y adolescentes | 5,0
6 | Que el set sea intercambiable | 4,7
14 | Que cada herramienta del set se justifique con una actividad pedagógica | 4,7
18 | Que no provoquen volcaduras del robot | 4,7
19 | Que las herramientas sean controlables por los mensajes Bluetooth | 4,7

Plataforma de control desde Windows
21 | Que se programen secuencias de las instrucciones soportadas por el robot | 4,7
24 | Que sea compatible con la aplicación actual de Android | 4,7

16 3.3 Definición de especificaciones

Tabla 3.2: Tabla de importancia relativa de las necesidades deseadas

Número | Necesidad | Importancia Relativa
| Programación del microcontrolador
2 | Que se utilice la misma base de máquina de estados actual | 4,3
5 | Que soporte la instrucción “if” con base en condiciones y sensores infrarrojos | 4,0
4 | Que soporte la instrucción “while” con base en condiciones y sensores infrarrojos | 3,7

Set de herramientas
9 | Que sea fácil de darle mantenimiento | 4,3
7 | Que las herramientas del set sean intercambiables a mano (no requiere herramientas). | 4,0
17 | Que sea barato de fabricar | 3,7

Plataforma de control desde Windows
20 | Que se comunique al robot utilizando Bluetooth Low Energy (BLE) con el protocolo GATT | 4,3
22 | Que se observe/simule la secuencia de instrucciones a ser enviadas al robot | 3,7
23 | Que se implemente utilizando Scratch | 3,7

Tabla 3.3: Tabla de importancia relativa de las necesidades aceptables

Número | Necesidad | Importancia relativa
| Set de herramientas
10 | Que los set sean fáciles de guardar y apilar | 3,3
15 | Que se cuenta con múltiples herramientas | 3,3
16 | Que se fabrique el cuerpo de la herramienta exclusivamente con piezas de acrílico de corte láser | 3,0

## 3.3 Definición de especificaciones

En continuación con la metodología propuesta, se desarrolla la definición de especificaciones que indican el qué medir para determinar si la propuesta o diseño cumple los requisitos. Para esto, a cada una de las necesidades indicadas en la sección anterior se le definen métricas que reflejen el grado de cumplimiento de las necesidades. Por lo cual, se da una búsqueda de

3 Metodología | 17

estándares, modelos o criterios que puedan ser aplicables a la necesidad y posteriormente, definir límites de cumplimiento ideal y marginales.

Definición de Métricas

Para cada necesidad identificada en el proyecto se buscó al menos un criterio de su cumplimiento en forma de normas, criterios técnicos o conceptuales. La asociación entre necesidad y métrica se presenta en matrices de asociación necesidad-métrica.

Valores ideales y marginales

Con las métricas definidas se requiere definir qué mediciones o rangos son aceptables para indicar que la necesidad se ha cumplido. Para esto se define el valor ideal (lo que se quiere que se logre) y el valor marginal (lo “mínimo” aceptable) para cada una de las métricas. Una tabla resumen de cada grupo se presenta a continuación, junto con las justificación de sus valores.

### 3.3.1 Definición de métricas, valores ideales y marginales de las especificaciones enfocadas en la programación del microcontrolador del robot

Se presenta en la tabla 3.4 las métricas propuestas para las necesidades enfocadas en la programación del microcontrolador del robot.

Tabla 3.4: Métricas propuestas para las necesidades enfocadas en la programación del microcontrolador del robot.

Número de métrica | Número de necesidad | Importancia relativa | Métrica | Unidad | Valor Marginal | Valor Ideal
1 | 1 | 5,0 | Operaciones afectadas por la implementación | Lista | Evasión de caídas y obstáculos | Vacía
2 | 2 | 4,7 | Se utiliza la estructura actual | Binario | Cumple | Cumple
3 | 3 | 4,3 | Se cumple con el estándar de programación | Binario | Cumple | Cumple
4 | 4 | 4,0 | Existe el soporte de la instrucción while | Binario | Cumple | Cumple
5 | 5 | 3,7 | Existe el soporte de la instrucción if | Binario | Cumple | Cumple

En la tabla 3.5 se muestra la matriz de correspodencia necesidades-métricas enfocadas en la programación del microcontrolador del robot.

18 3.3 Definición de especificaciones

Tabla 3.5: Matriz de correspondencia entre necesidades y métricas de enfocadas en la programación del microcontrolador del robot

| Metrica
Necesidad | 1 | 2 | 3 | 4 | 5
1 | x
2 | | x
3 | | | x
4 | | | | x
5 | | | | | x

Operaciones afectadas por la implementación

Esta métrica se toma como la lista de las operaciones que dejen de funcionar, debido a las modificaciones de código propuestas. Idealmente, un robot con las modificaciones propuestas por este proyecto debe mantener su funcionamiento y compatibilidad previas. Esto se vería como un robot con el código modificado, el cual mantendría su compatibilidad con todos los comandos de la aplicación Android actual, que puede realizar todos los movimientos actuales y mantiene los comportamientos de evasión/seguridad actualmente programados. De manera marginal, se define que la funcionalidad de “evitar caídas” puede ser incompatible o desactivada, debido al uso simultáneo de los sensores infrarrojos de la propuesta.

Se utiliza la estructura actual

Esta métrica se refiere a que el robot actualmente posee una arquitectura de lectura y ejecución de instrucciones en base a una máquina de estados [7] y se desea que se mantenga, por lo que las modificaciones del código para cumplir esta necesidad deben estar alineadas con la estructura de la máquina de estados y el estándar de instrucciones ya presentes.

Se cumple con el estándar de programación

Esta métrica se refiere al estándar de programación utilizado por el laboratorio GIRoM [38] en sus proyectos, indica el formato de las funciones, variables y comentarios. El código propuesto de solución debe seguir estas indicaciones.

Existe el soporte de la instrucción while

Esta métrica se refiere a que el código modificado permita crear ciclos “while” con base en condiciones de alto y bajo de la lecturas de los sensores infrarrojos del robot en los set de instrucciones enviados por BLE.

3 Metodología | 19

Existe el soporte de la instrucción if

Esta métrica se refiere a que el código modificado permita crear bifurcaciones con condicionales “if” con base en condiciones de alto y bajo de la lecturas de los sensores infrarrojos del robot en los set de instrucciones enviados por BLE.

### 3.3.2 Definición de métricas, valores ideales y marginales de las especificaciones enfocadas en el hardware del robot

Por su parte, se presentan en la tabla 3.6 el resumen de las especificaciones enfocadas en el hardware del robot.

Tabla 3.6: Métricas propuestas para las necesidades enfocadas en el hardware del robot

Número de métrica | Número de necesidad | Importancia relativa | Métrica | Unidad | Valor Marginal | Valor Ideal
6 | 6 | 4,7 | Cantidad de acciones para utilizar una herramienta diferente | Acciones | <=16 | <=4
7 | 7 | 4,0 | Equipo necesario para el intercambio | Lista | Destornillador, Pinzas | Vacía
8 | 8 | 5,0 | Cantidad de acciones para realizar el ensamble | Acciones | <=64 | <=16
9 | 9 | 4,3 | piezas de reemplazo Disponibilidad de | Lista | Disponibles en tiendas, corte láser, impresión 3d | Disponibles en tiendas
10 | 9 | 4,3 | Acciones requeridas de mantenimiento | Lista | Limpieza, engrasados simples anuales, almacenamiento específico | Limpieza
11 | 10 | 3,3 | Cantidad de acciones para guardar los sets | Acciones | <=8 | <=2
12 | 10 | 3,3 | Volumen requerido para apilar dos sets | cmˆ3 | <=9000 | <=3000
13 | 11 | 5,0 | Elementos del robot que requieran ser desarmados al ralizar el cambio de herramienta | Lista | Carcasa, Marcador | Vacía
14 | 12 | 5,0 | Protección ante impacto según peso del robot (en base a normativa IK) | Julios | 3=< | 5=<
15 | 13 | 5,0 | Cumpla con los requisitos de AGE DETERMINATION GUIDELINES de SPSC | Binario | Cumple | Cumple
16 | 14 | 5,0 | Actividad provista por herramienta | Binaria | Cumple | Cumple
17 | 15 | 4,7 | Cantidad de efectores implementados | Cantidad | 1 | >=2
18 | 16 | 3,3 | Elementos del ensamble fabricado u obtenido por otros métodos. | Lista | Elementos de torsión, elementos de adhesion | Vacía
19 | 17 | 3,7 | Cantidad de dinero para obtener las piezas del ensamble | USD | <=30 | <=15
20 | 18 | 4,7 | Efecto del desplazamiento del centro de masa en operación de la herramienta | Lista | Inestabilidad sin volcamiento | Vacio
21 | 19 | 4,7 | Se logra controlar la herramienta por comandos | Binaria | Cumple | Cumple

20 3.3 Definición de especificaciones

En la tabla 3.7 se muestra la matriz necesidades-métricas enfocadas en el hardware del robot.

Tabla 3.7: Matriz de correspondencia entre necesidades y métricas de enfocadas en el hardware del robot

| Métrica
Necesidad | 6 | 7 | 8 | 9 | 10 | 11 | 12 | 13 | 14 | 15 | 16 | 17 | 18 | 19 | 20 | 21
6 | x
7 | | x
8 | | | x
9 | | | | x | x
10 | | | | | | x | x
11 | | | | | | | | x
12 | | | | | | | | | x
13 | | | | | | | | | | x
14 | | | | | | | | | | | x
15 | | | | | | | | | | | | x
16 | | | | | | | | | | | | | x
17 | | | | | | | | | | | | | | x
18 | | | | | | | | | | | | | | | x
19 | | | | | | | | | | | | | | | | x

Cantidad de acciones para utilizar una herramienta diferente

Esta métrica se refiere a cuántos pasos o acciones deben tomarse en cuenta para lograr remover una herramienta colocada e instalar una segunda herramienta ensamblada. Las acciones se basan en la idea de una guía de uso de usuario o de armado de LEGOS, donde se muestra paso a paso el proceso de intercambio. El valor ideal de menos de cuatro se basa en una secuencia simple de intercambiar un diseño como el broche de plástico por otro.

Equipo necesario para el intercambio

Esta métrica se refiere a las herramientas necesarias para cambiar la herramienta en uso. Idealmente, el diseño del set permite hacer el intercambio, sin utilizar ninguna herramienta y de valor marginal la lista incluye herramientas simples como destornilladores o pinzas.

Cantidad de acciones para realizar el ensamble

Esta métrica se refiere a cuántas acciones o pasos se requiere para ensamblar cada una de las herramientas del set. Las acciones se basan en la idea de una guía de uso de usuario o de armado de LEGOS, donde se muestra paso a paso el proceso del ensamble de la herramienta. El valor ideal de 8 o menos se basa en tener un ensamble con la colocación de dos puntos de sujeción articuladas (4 acciones), un elemento de transmisión de potencia (2 acciones) y un

3 Metodología | 21

elemento de interacción (2 acciones). El valor marginal se tiene de 24 o menos para expandir las piezas en el ensamble, pero de ser muy restrictivo en el diseño puede expandirse.

Disponibilidad de piezas de reemplazo

Esta métrica se refiere a la facilidad de obtención de las piezas utilizadas en el set, en el caso de que se dañen y se necesiten reemplazarlas. Idealmente, todas las piezas del set son estándares que se consiguen en tiendas del país. Marginalmente, las piezas se pueden obtener por servicios de impresión 3d y corte láser locales, ya que los diseños (pdfs o cads respectivamente) serían públicos.

Acciones requeridas de mantenimiento

Esta métrica se refiere a las acciones que deberán realizar los usuarios para darle mantenimiento a los componentes en las escuelas y colegios. Idealmente, los diseños solo requieren limpieza para que el polvo no dañe o interfiera en los elementos mecánicos o electrónicos. Marginalmente, ciertos componentes mecánicos de trasmisión o articulación podrían requerir un engrasado simple (uso de W40 por ejemplo) o un almacenamiento específico (como en cajas selladas) para protección ambiental para evitar corrosión o un daño mecánico.

Lista de acciones para guardar los sets

Esta métrica se refiere a la cantidad de acciones que deben tomar las escuelas y colegios para almacenar apropiadamente las herramientas de los sets. Idealmente, las herramientas podrán ser removidas del robot y directamente almacenadas en un armario (2 acciones). Marginalmente, las herramientas requerirán un orden, posición o incluso, una remoción de elementos para un guardado seguro, por lo que, se limita a 8 acciones para excluir el que se requiera desarmar las herramientas completamente.

Volumen requerido para apilar dos sets

Esta métrica se refiere a la cantidad de espacio requerido para guardar un par de set de herramientas. Idealmente se tienen menor a 3000 cm³
, basado en un estuche de mano de 7x15x25 cm³
. Marginalmente, se toma el triple de este valor como requerido para guardar el set, basándose en una caja pequeña de 21 cm de altura con una misma base similar al estuche de referencia.

Protección ante impacto según peso del robot

Esta métrica se refiere a la resistencia mecánica de las herramientas. En el trabajo previo sobre el robot se [8] utilizó de referencia la normativa IK08 (5J). al estimar energías de impacto de 3J como referencia para una caída del robot desde 90 cm. Por lo tanto, como

22 3.3 Definición de especificaciones

ideal se busca mantener el mismo grado de cumplimiento del IK08 y como marginal que la herramienta resista un impacto del robot actual.

Cumpla con los requisitos de AGE DETERMINATION GUIDELINES de CPSC

Esta métrica se refiere a utilizar la guía del “Consumer Product Safety Commision” (CPSC) de Estados Unidos de América con su documento “AGE DETERMINATION GUIDELINES: Relating Consumer Product Characteristics to the Skills, Play Behaviors, and Interests of Children” [39] que presenta guías y tablas de las características de los distintos “juguetes” para las distintas edades. Como referencia se utiliza los 6 años en adelante y las categorías de producto de “building play”, que pueden armar y desarmar el robot hasta cierto punto.

Actividad provista por herramienta

Esta métrica se refiere a la existencia de una actividad pedagógica para la justificación de la implementación de las herramientas diseñadas para el set.

Elementos del ensamble fabricado u obtenido por otros métodos

Esta métrica busca que las herramientas sean fabricadas mayormente por elementos de obtenidos en corte láser, por lo tanto, se busca medir cuáles elementos del diseño requieren otro método de fabricación o de obtención en cada una de las propuestas. Idealmente, la lista sería vacía en el caso que la estructura completa se pueda ensamblar con piezas de corte láser. Por su parte, la lista marginal incluye elementos de sujeción y torsión para que las herramientas puedan utilizar elementos como tornillos y ejes comprados o impresos en 3d en su ensamble.

Cantidad de dinero para obtener las piezas del ensamble

Esta métrica se refiere al costo de comprar y fabricar todos los componentes necesarios para armar individualmente cada una de las herramientas. Por lo tanto, ayuda a decidir cuáles diseños de herramienta son más “rentables” para su implementación y distribución en relación con el costo total del robot de $175. Su valor ideal y marginal son de $15 y $30

respectivamente.

Efecto del desplazamiento del centro de masa en operación de la herramienta

Este métrica se refiere al efecto que tiene el uso de la herramienta en la estabilidad del robot dada la modificación del centro de masa del robot. La atención a esta variable se da porque el control de movimiento, así como su estabilidad dependen de ella, por lo tanto, se busca diseños de herramientas y actividades que no comprometan la funcionalidad del robot, al limitar el desplazamiento de su centro de masa entre sus tres puntos de contacto

3 Metodología | 23

con el suelo (sus tres llantas) que forma un triángulo de 12 cm de hipotenusa y 8 cm de catetos a 5 cm de distancia del borde del chasis. Por lo tanto, como valor ideal se busca que el desplazamiento no provoque ningún efecto (Lista vacía) al operar las herramientas y como marginal una inestabilidad inercial, sin llegar a la volcadura, esto puede verse como la tercera llanta perdiendo el contacto con el suelo temporalmente al frenar o acelerar.

Se logra controlar la herramienta por comandos

Esta métrica se refiere a que la funcionalidad de cada una de las herramientas esté integrada en la máquina de estados de instrucciones del robot y se opere mediante los comandos que recibe por BLE.

### 3.3.3 Definición de métricas, valores ideales y marginales de las especificaciones enfocadas en la plataforma de control de robot desde Windows

Por último, se presentan en la tabla 3.8 el resumen de las especificaciones enfocadas en la plataforma de control de robot desde Windows.

Tabla 3.8: Métricas propuestas para las necesidades enfocadas en la plataforma de control de robot desde Windows

Número de métrica | Número de necesidad | Importancia realtiva | Métrica | Unidad | Valor Marginal | Valor Ideal
22 | 20 | 4,3 | Utiliza el protocolo BLE GATT | Binario | Cumple | Cumple
23 | 21 | 4,7 | Funciones del robot soportadas al programar | Lista | MOV, ROT, PEN, TOOL, FOR, WHILE,IF, EVA | MOV, ROT, PEN, TOOL, FOR, WHILE,IF, EVA
24 | 22 | 3,7 | soportadas al simular Funciones del robot | Lista | MOV, ROT, PEN, FOR, WHILE,IF | MOV, ROT, PEN, TOOL, FOR, WHILE,IF, EVA
25 | 23 | 3,7 | Uso de Scratch como base | Binario | Cumple | Cumple
26 | 24 | 4,7 | Capacidades soportadas | Lista | Importar | Importar, Exportar

En la tabla 3.9 se muestra la matriz necesidades-métricas enfocadas en la plataforma de control de robot desde Windows.

24 3.3 Definición de especificaciones

Tabla 3.9: Matriz de correspondencia entre necesidades y métricas enfocadas en la plataforma de control de robot desde Windows

| Métrica
Necesidad | 22 | 23 | 24 | 25 | 26
20 | x
21 | | x
22 | | | x
23 | | | | x
24 | | | | | x

Utiliza el protocolo BLE GATT

Esta métrica se refiere al requisito de utilizar la tecnología Bluetooth Low Energy (BLE) con el protocolo estandarizado GATT para realizar la comunicación entre la plataforma Windows y el robot.

Funciones del robot soportadas al programar

Esta métrica se refiere al soporte de las acciones que se le pueden enviar al robot, al programar desde la plataforma de Windows. Actualmente, el robot tiene una lista de acciones que es capaz de realizar y ser controlada desde la aplicación Android:

- Movimiento recto (adelante y atrás)
- Movimiento rotacional (derecha izquierda)
- Control de lápiz (Marcador arriba y abajo)
- For (Ciclo de cantidad de veces)
- Evasión de caídas (on/off)
- Evasión de objetos (on/off)

Con la expansión del set de instrucciones de este trabajo se incluyen:

- While (Ciclo condicional de los sensores infrarrojos)
- If (Branch condicional de los sensores infrarrojos)
- Control de herramientas (operación del actuar según la herramienta seleccionada)

De manera ideal y marginal todas las instrucciones se le envían al robot desde la plataforma de Windows.

Funciones del robot soportadas al simular

Esta métrica se refiere al soporte de las acciones del robot que se pueden simular, al programar desde la plataforma de Windows. Actualmente, el robot tiene una lista de acciones que es capaz de realizar y ser simuladas desde la aplicación Android:

3 Metodología | 25
- Movimiento recto (adelante y atrás)
- Movimiento rotacional (derecha izquierda)
- Control de lápiz (Marcador arriba y abajo)
- For (Ciclo de cantidad de veces)

Con la expansión del set de instrucciones de este trabajo se incluyen:

- While (Ciclo condicional de los sensores infrarrojos)
- If (Branch condicional de los sensores infrarrojos)
- Control de herramientas (operación del actuar según la herramienta seleccionada)

De manera ideal todas las instrucciones anteriores del robot se simulan desde la plataforma de Windows. De manera marginal, se excluyen las acciones de herramienta, dado el requerimiento de programar el objeto con el que interactúa la herramienta.

Uso de Scratch como base

Esta métrica se refiere a si se utiliza la plataforma de Scratch [22] en el proceso del desarrollo del control del robot desde Windows.

Capacidades soportadas

Esta métrica se refiere a las capacidades que se le da a la aplicación de control desde Windows de compatibilidad con la aplicación de control desde Android. En el caso ideal, puede importar archivos desde la aplicación Android para cargar un algoritmo realizado en Android y exportar el logaritmo realizado en la aplicación de Windows a la aplicación Android. Por su parte, el marginal toma solo la capacidad de importar el algoritmo desde la aplicación Android, debido a que zl exportar podría requerir el modificar la aplicación Android y se saldría del alcance de este proyecto.

## 3.4 Generación de conceptos

Continuando con la metodología, ahora se busca explorar sistemáticamente conceptos solución que puedan cumplir con las necesidades. Para este fin se realiza una descripción funcional del sistema a diseñar, así como los subproblemas que implica su funcionamiento para explorar e investigar conceptos dirigida y ordenadamente.

### 3.4.1 Organización de subproblemas

Primero, para cada uno de los subsistemas en los que se está trabajando, se realiza una descripción funcional para describir cuáles son sus salidas y entradas en términos de energía, materia y señales.

26 3.4 Generación de conceptos

Por lo que, a continuación se presenta el diagrama funcional de caja negra de la modificación a la programación del robot en la fig.3.1, el del set de herramientas en la fig.3.2 y el de la plataforma de control desde Windows en la fig.3.3.

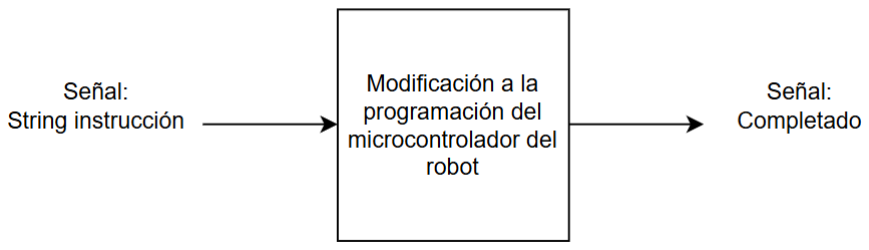
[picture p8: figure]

Figura 3.1: Diagrama funcional de caja negra de la modificación al código del robot

Como se observa en el diagrama anterior, para la modificación del código funcionalmente solo se cuenta con una señal de entrada, siendo esta el string de comandos recibida por Bluetooth y una salida, indicándole a la máquina de estados que se completó con la instrucción.

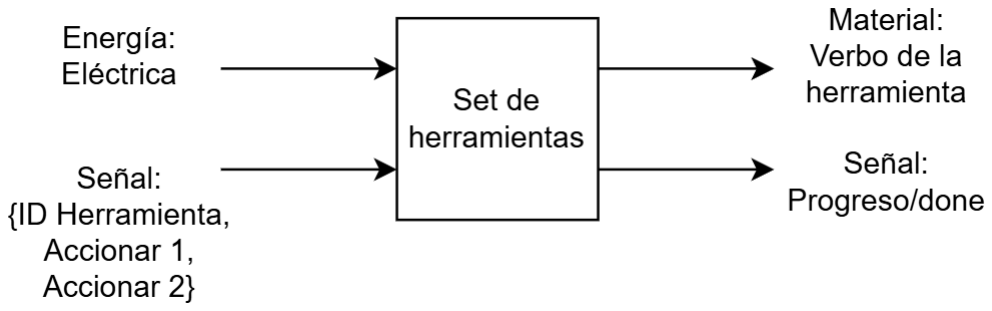
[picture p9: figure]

Figura 3.2: Diagrama funcional de caja negra del set de herramientas

Como se observa en el diagrama anterior, para el diseño del set de herramientas funcionalmente se tiene dos entradas, una de energía eléctrica para alimentar el motor y generar el movimiento de la herramienta y una señal de control en referencia a la herramienta que se está utilizando, así como la acción que debe hacer la herramienta. De salida material se tiene el verbo de la herramienta (La acción que realiza, una garra: agarró/soltó, un elevador: elevó/descendió, etc.) y una señal lógica para indicarle a la máquina de estados del robot que la acción se ha completado y puede continuar.

3 Metodología | 27

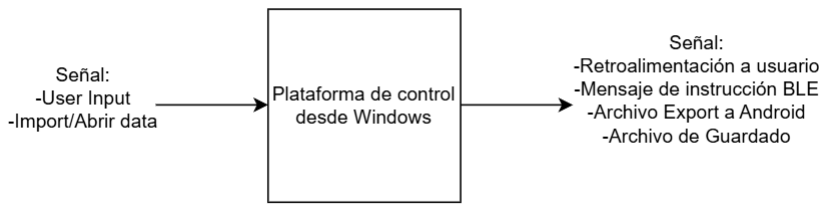
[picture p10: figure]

Figura 3.3: Diagrama funcional de caja negra de la aplicación de control desde Windows

Como se observa en el diagrama anterior, para el diseño de la aplicación de control desde Windows se tiene de entrada dos clases de señales, aquella de “user input” (para agregar comandos, tomar acciones, etc.) y las de archivos de datos para abrir/importar proyectos. Por su parte, de salida se tiene una lista de señales:

- Retroalimentación al usuario: formas de saber qué esta haciendo el software, si tiene problemas, qué ha programado etc, a través de gráficos (GUI).
- Mensaje de instrucción BLE: Un string con los comandos del robot ha ser trans-

mitido por BLE.
- Archivo de exportación a Android: Algún archivo que la aplicación de Android

pueda abrir para cargar un algoritmo trabajado en la aplicación Windows.
- Archivo de Guardado: Un archivo que la aplicación Windows pueda abrir para

continuar trabajando en un proyecto previamente iniciado desde la aplicación.

Dadas las definiciones previas de entradas y salidas requeridas de los diseños, se procede a desarrollar en subproblemas el proceso de obtener las salidas con base en las entradas indicadas.

A continuación, se presentan los diagramas funcionales de subproblemas de la modificación de la programación del microcontrolador del robot en la fig. 3.4, del set de herramientas en la fig. 3.5 y de la plataforma de control desde Windows en la fig. 3.6.

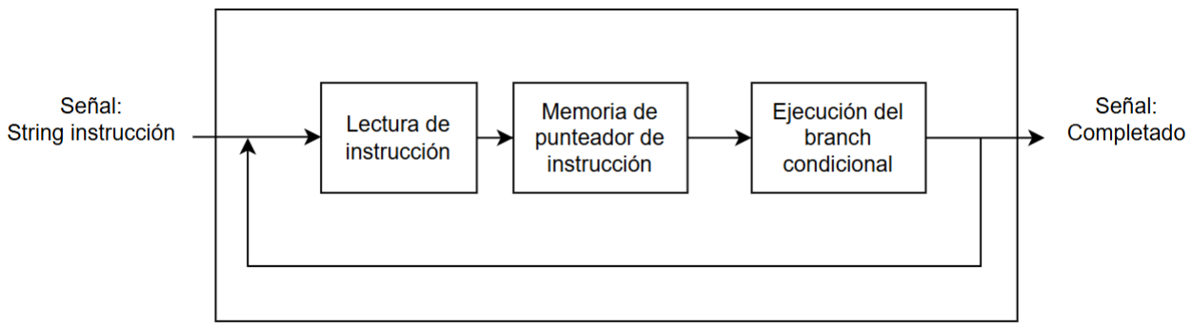
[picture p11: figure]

Figura 3.4: Diagrama funcional de subproblemas de la modificación de la programación del microcontrolador del robot

En el diagrama anterior se observa que se tienen tres subproblemas: primero, el como “leer”

28 3.4 Generación de conceptos

o decodificar la instrucción del string de instrucciones. Segundo, al leer una instrucción de bifurcación lógica (if, while) se necesita un método para “saber” la posición del puntero en el inicio y final de estos segmentos en el string de instrucciones. Tercero, el cómo modificar el punteador de la lectura de la instrucción con base en los estados de los sensores (While repiten o saltan segmentos, mientras los if pueden saltarse segmentos).

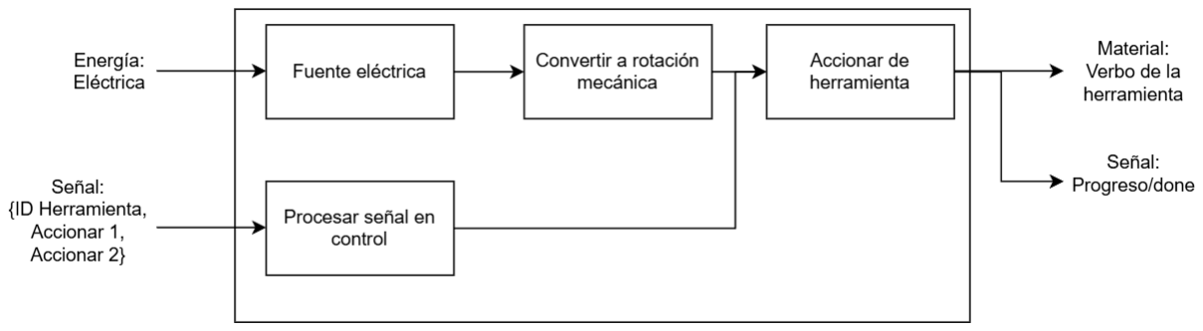
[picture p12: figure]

Figura 3.5: Diagrama funcional de subproblemas del set de herramientas

Para el caso del diseño del set de herramientas se observa del diagrama anterior los subproblemas de:

- Fuente eléctrica: dónde o cómo se obtendrá la energía para alimentar a la herra-

mienta.

- Convertir a rotación mecánica: la manera de cómo convertir la energía eléctrica

en rotación mecánica para activar los mecanismos del set, más allá de qué clase de motor, es cómo diseñar para tener una fuente de movimiento para una variedad de mecanismos.

- Accionar de herramienta: ya teniendo una fuente de movimiento, el cómo usarla para realizar una acción. Aquí es donde se detallan los distintos “efectores” del set (el mecanismo que logra que la garra agarre/suelte, etc.).
- Proceso de señal de control: dada la señal obtenida del string de instrucción, el

cómo se convierte en señales eléctricas para que el sistema realice la acción deseada.

3 Metodología | 29

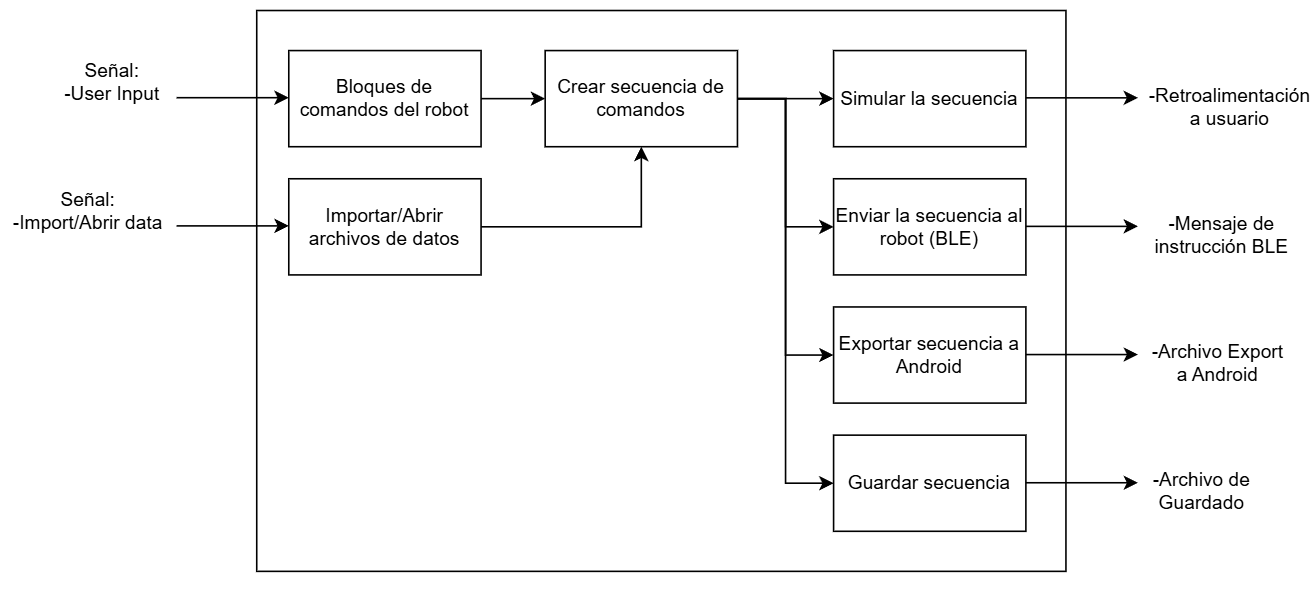
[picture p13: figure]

Figura 3.6: Diagrama funcional de subproblemas de la plataforma de control desde Windows

Del diagrama anterior, se obtienen los siguientes subproblemas:

- Bloques de comandos del robot: el input del usuario sea procesado en bloques, al

realizar la programación. Por lo que, deben existir bloques para cada instrucción y acción que el usuario necesite.

- Importar/Abrir archivos de datos: debe haber una funcionalidad que le permita al

usuario continuar proyectos previos iniciados en Windows o Android..

- Crear secuencias de comandos: se refiere a que los archivos e inputs de usuarios pueden

crear secuencias de múltiples comandos, combinándose en largas instrucciones.

- Simular la secuencia: se refiere a que se pueda observar de manera gráfica el compor-

tamiento resultante de la secuencia de comandos.

- Enviar la secuencia al robot (BLE): se refiere a que se pueda transmitir el string de

comandos al robot mediante BLE.

- Exportar secuencia a Android: se refiere a que exista algún método de continuar el

trabajo de la aplicación Windows en la aplicación Android al transmitir un archivo.

- Guardar secuencia: se refiere a que exista un método para crear un archivo que permita

continuar un proyecto en la misma o computadora diferente.

### 3.4.2 Conceptos solución propuestos

La modificación de la programación del microcontrolador del robot

Dado que el código del microcontrolador del robot ha sido diseñado desde cero durante múltiples proyectos del laboratorio GIRoM sin utilizar una base o estándar externo, no

30 3.4 Generación de conceptos

existen paquetes o proyectos de terceros que sean inmediatamente compatibles con la arquitectura de control actualmente presente en la plataforma para solventar los subproblemas y las necesidades de esta parte del proyecto. Por lo tanto, se decide de manera directa implementar desde cero funciones que resuelvan directamente el manejo de la memoria del punteador de la instrucción, así como funciones que modifiquen el punteador según los cuatro posibles casos de lectura de los sensores dentro de las máquinas de estados actual y para resolver “la lectura de la instrucción” se decide modificar la función actual que reconoce las instrucciones para cambios de estados, agregándole a la lista de instrucciones/estados reconocidos un iniciador de ciclo, un finalizador de ciclo, un indicador de condicional y un indicador de salto.

El set de herramientas

Para los conceptos del set de herramientas, primero se decide tomar por aparte el subproblema “Procesar señal de control”, ya que es parte de la programación en el microcontrolador y se decide resolverlo agregando un estado que ejecute el control de la herramienta, en función del actuador seleccionado más adelante.

Cabe aclarar que, debido a limitaciones de pines disponibles en el microcontrolador, el diseño se limita a un solo actuador.

Para el siguiente subproblema de ”Fuente eléctrica” se poseen tres conceptos:

1. Alimentación directa del microcontrolador: la tarjeta utilizada por el AttaBot-STEM (La IDEADBOARD) posee una configuración de pines que permite conectar directamente VCC y GROUND junto con cualquier pin de uso general. Por lo que, equipos como servomotores o conexiones similares pueden conectarse fácilmente y con la limitación de recibir alimentación de 3.3V
2. Alimentación de la batería de los motores: El diseño actual del Attabot-STEM utiliza un arreglo de batería-booster para aumentar la tensión de alimentación de los motores de las ruedas del Attabot-STEM mediante los drivers de la IDEABOARD. Realizando un pequeño circuito para compartir este nodo, puede utilizarse como una fuente para la herramienta a 5V.
3. Alimentación por batería propia: A costa de aumentar el precio y el peso, se puede utilizar una batería recargable de tensión superior para aumentar el torque posible y la modularidad del diseño, al disminuir las conexiones eléctricas nuevas entre elementos, al separar sus fuentes de energía.

Para escoger el concepto ganador, primero se realiza un filtrado en la tabla 3.10. Se toma el concepto de la conexión directa del microcontrolador como concepto de referencia y se compara de manera positiva (1) o negativa (-1) los otros conceptos.

3 Metodología | 31

Tabla 3.10: Filtrado de los conceptos para el subproblema de Fuente eléctrica

Conceptos
Criterio de selección | Fuente eléctrica Directa del Batería de los Batería microcontrolador motores (boost) propia
Facilidad de ensamble Facilidad de intercambio Facilidad de mantenimiento Facilidad de guardado Resistencia Seguridad Afectación a la distribución del peso Precio | 0 -1 -1 0 -1 -1 0 0 -1 0 0 -1 0 0 -1 0 0 -1 0 0 -1 0 0 -1
Suma + Suma 0 Suma - | 0 0 0 8 6 0 0 2 8
Neto | 0 -2 -8
Orden Pasa: | 1 2 3 Sí Sí No

Del proceso anterior se observa que mientras las tres conexiones provean la potencia suficiente, el utilizar la batería propia se compara de manera significativamente negativa en relación con las otras opciones, por lo tanto, se filtra del proceso de selección.

Como siguiente paso se realiza una comparación para seleccionar el concepto ganador a este subproblema en la tabla 3.11. Cabe aclarar que, el peso se obtuvo de la distribución de importancia relativa de las necesidades y la calificación asignada a cada concepto, se basa en la estimación de esta escala:

1) Se toma como significativamente peor que la referencia.
2) Se toma como un poco peor que la referencia.
3) Se toma como la referencia.
4) Se toma como un poco mejor que la referencia.
5) Se toma como significativamente mejor que la referencia.

32 3.4 Generación de conceptos

Tabla 3.11: Selección de los conceptos para el subproblema de la Fuente eléctrica

Conceptos
Fuente eléctrica
Criterio de selección | Peso | Directa del microcontrolador | Batería de los motores (boost)
| | Calificación Evaluación ponderada | Calificación Evaluación ponderada
Facilidad de ensamble Facilidad de intercambio Facilidad de mantenimiento Facilidad de guardado Resistencia Seguridad Afectación a la distribución del peso Precio | 14,02% 13,08% 12,15% 9,35% 14,02% 14,02% 13,08% 10,28% | 3 0,421 3 0,393 3 0,364 3 0,280 3 0,421 3 0,421 3 0,393 3 0,308 | 2 0,280 2 0,262 3 0,364 3 0,280 3 0,421 3 0,421 3 0,393 3 0,308
Total de puntos Lugar | | 3,000 1 | 2,729 2
Desarrollo | | Sí | No

De esta tabla de selección se concluye asumiendo que el método que ofrezca la suficiente potencia y la conexión directa al microcontrolador es el concepto ganador.

Para el siguiente subproblema de “Convertir a rotación mecánica” se tienen los siguientes conceptos:

1. Motor CD + Driver: permite que con el uso de dos pines controlar la dirección y velocidad en lazo abierto, así como alimentar el motor de manera independiente.
2. Servomotor 180: permite una conexión simple al microcontrolador y a fuentes externas con poca manipulación. Permite un control comparativamente preciso de la posición, pero con la limitante de solo contar con media rotación como espacio de trabajo.
3. Servomotor 360: también conocido como “servomotor continuo”, utiliza la misma conexión y control simple que un servomotor. Así como la opción de ser alimentado por fuentes externas con poca manipulación. La ventaja se da en que este motor rota de manera continua y su control se da sobre la dirección y velocidad mediante un solo PWM.
4. Motor a pasos + Driver: esta configuración (con el Driver apropiado) permite controlar el motor con el uso de 2 pines del microcontrolador. Una señal para dirección

3 Metodología | 33

y otra para indicar el paso. Esto permite tener un control relativamente preciso de la posición y velocidad. Con la desventaja de tener una mayor precio y peso de las otras opciones.

Para escoger el concepto ganador, primero se realiza un filtrado en la tabla 3.12. Se toma el concepto de Motor CD + Driver como concepto de referencia y se compara de manera positiva (1) o negativa (-1) los otros conceptos.

Tabla 3.12: Filtrado de los conceptos para el subproblema de Convertir a rotación mecánica

Conceptos
Criterio de selección | Convertir a rotación mecánica Motor CD Servomotor Servomotor Motor a pasos + Driver 180 360 + Driver
Facilidad de ensamble Facilidad de intercambio Facilidad de mantenimiento Facilidad de guardado Resistencia Seguridad Afectación a la distribución del peso Precio | 0 1 1 0 0 1 1 0 0 1 1 0 0 1 1 -1 0 0 0 0 0 0 0 0 0 0 0 -1 0 0 0 -1
Suma + Suma 0 Suma - | 0 4 4 0 8 4 4 5 0 0 0 3
Neto | 0 4 4 -3
Orden Pasa: | 3 1 1 4 No Sí Sí No

Para reducir la cantidad de combinaciones a evaluar más adelante y por criterios técnicos, de los conceptos anteriores se descarta el concepto 4, debido al peso de los motores a paso y al precio de los motores y drivers requeridos, por lo que, ambas características limitan en exceso el resto del diseño en un contexto donde las ventajas de un motor a pasos son mínimas comparadas a las alternativas.

Además, se descarta el concepto 1, ya que los conceptos 3 y 2 poseen una ventaja técnica muy superior al concepto 1, al solo requerir un pin para su control, se deja el espacio de diseño a futuro para herramientas con sensores, para implementar un segundo actuador en el set o cualquier otro uso que se le pueda dar al recurso limitado de los pines de uso general del microcontrolador.

34 3.4 Generación de conceptos

Como siguiente paso se realiza una comparación para seleccionar el concepto ganador a este subproblema en la tabla 3.13 con la misma escala previamente descrita.

Tabla 3.13: Selección de los conceptos para el subproblema de Convertir a rotación mecánica

Conceptos
Convertir a rotación mecánica
Criterio de selección | Peso | Servomotor 180 | Servomotor 360
| | Calificación Evaluación ponderada | Calificación Evaluación ponderada
Facilidad de ensamble Facilidad de intercambio Facilidad de mantenimiento Facilidad de guardado Resistencia Seguridad Afectación a la distribución del peso Precio | 14,02% 13,08% 12,15% 9,35% 14,02% 14,02% 13,08% 10,28% | 3 0,421 3 0,393 3 0,364 3 0,280 3 0,421 3 0,421 3 0,393 3 0,308 | 4 0,561 3 0,393 3 0,364 3 0,280 3 0,421 3 0,421 3 0,393 3 0,308
Total de puntos Lugar | | 3,000 2 | 3,140 1
Desarrollo | | No | Sí

Por último, los servomotores 180 y 360 a nivel de precio, tamaño, peso e instalación son lo mismo. Su diferencia radica en el control y el diseño mecánico que cada uno permite. Por lo tanto, por criterio de diseñador se considera que el servomotor 360 permite diseño de ensambles de herramientas más flexible y simple, ya que por medio de topes mecánicos en el diseño y calibración del tiempo de activación, se puede realizar un control de posición a lazo abierto que en este contexto de un robot educativo de bajo costo es aceptable y la libertad de realizar revoluciones infinitas mantiene abierta la posibilidad de implementación de más mecanismos.

Para el siguiente subproblema de ”Accionar de Herramientas” se tienen de conceptos:

1. Configuraciones de robot: para cada herramienta, el ensamble del robot es modificado para que permita el funcionamiento. El robot tendría instrucciones de cómo armarlo para utilizar el “modo grúa”, “modo garra”, etc.
2. Herramientas por módulos: las herramientas se arman de manera independiente con sus respectivos elementos mecánicos. Se realiza un diseño de “slots” modulares que permite intercambiar una herramienta por otra en un mismo espacio del robot.

3 Metodología | 35

Por ejemplo, ensamblando las herramientas en diferentes tapas del robot y para intercambiarlas se intercambia el modulo entero de esta tapa con la herramienta deseada. El robot tendría “el módulo de grúa”, “el módulo de garra”, etc.

3. Herramientas por piezas: Se diseñan piezas que se conectan entre ellas (estilo los set de LEGO Robotics) y se realizan diseños que reutilizan los elementos para armar las distintas herramientas sobre una base común. Para este caso, el robot tendría una base que se le adhiere al chasis sobre la cual se arma el mecanismo de “grúa” o de “garra” siguiendo instrucciones de ensamblaje.
4. Módulos de piezas: combinación de los conceptos de 2 y 3. Se crean módulos que se pueden instalar y remover en su totalidad sobre el diseño actual del robot. El diseño de “grúa” y de “garra” utilizan piezas en común (manteniendo la idea de los set de LEGO), pero se ensamblan en sus propios módulos para simplificar el intercambio.

Para escoger el concepto ganador, primero se realiza un filtrado en la tabla 3.14. Se toma el concepto de Configuraciones de robot como concepto de referencia y se compara de manera positiva (1) o negativa (-1) los otros conceptos.

Tabla 3.14: Filtrado de los conceptos para el subproblema del Accionar de Herramientas

Conceptos
Criterio de selección | Accionar de Herramientas Configuraciones Herramientas Herramientas Módulos de robot por módulos por piezas de piezas
Facilidad de ensamble Facilidad de intercambio Facilidad de mantenimiento Facilidad de guardado Resistencia Seguridad Afectación a la distribución del peso Precio | 0 1 0 1 0 1 1 1 0 1 1 1 0 0 1 1 0 0 0 0 0 0 0 0 0 -1 0 0 0 0 1 1
Suma + Suma 0 Suma - | 0 3 4 5 8 4 4 3 0 1 0 0
Neto | 0 2 4 5
Orden Pasa: | 4 3 2 1 No Sí Sí Sí

36 3.4 Generación de conceptos

Del filtrado anterior, se concluye que el concepto de utilizar Configuración del robot se compara de manera negativa antes de las otras alternativas, por lo tanto, se elimina del proceso de selección.

Para continuar con el proceso de selección del concepto ganador al subproblema de Accionar de Herramientas, se presenta en la tabla 3.15 la comparativa para la selección utilizando la escala previamente detallada.

Tabla 3.15: Selección de los conceptos para el subproblema de Accionar de Herramientas

Conceptos
Accionar de Herramientas
Criterio de selección | Peso | Herramientas por módulos | Herramientas por piezas | Módulos de piezas
| | Calificación Evaluación ponderada | Calificación Evaluación ponderada | Calificación Evaluación ponderada
Facilidad de ensamble Facilidad de intercambio Facilidad de mantenimiento Facilidad de guardado Resistencia Seguridad Afectación a la distribución del peso Precio | 14,02% 13,08% 12,15% 9,35% 14,02% 14,02% 13,08% 10,28% | 3 0,421 4 0,523 2 0,243 2 0,187 3 0,421 3 0,421 3 0,393 2 0,206 | 3 0,421 2 0,262 3 0,364 3 0,280 3 0,421 3 0,421 3 0,393 3 0,308 | 3 0,421 3 0,393 3 0,364 3 0,280 3 0,421 3 0,421 3 0,393 3 0,308
Total de puntos Lugar | | 2,813 3 | 2,869 2 | 3,000 1
Desarrollo | | No | No | Sí

Como resultado de la tabla de selección se observa como la combinación de conceptos de utilizar el IDEABOARD como fuente de energía y ensamblar el set de herramientas en módulos de piezas resultan en los conceptos más simples de ensamblar, intercambiar y mantener, al utilizar piezas en común entre efectores.

La plataforma de control desde Windows

Dada la naturaleza del sistema de control de Windows de ser solamente software, se tienen tres vertientes de los conceptos solución:

1. Diseñar y programar desde cero una aplicación con las características necesarias.
2. Tomar una aplicación Windows ya existente que posea funcionalidades deseadas y modificarla para que cumpla las necesidades faltantes.
3. Portar la aplicación Android existente a Windows.

3 Metodología | 37

Por razones de practicabilidad y tiempo del proyecto el concepto 1 se descarta. El concepto 3 implicaría reescribir la aplicación en un lenguaje compatible con Windows, actualmente la aplicación fue construida en Kotlin, por lo que, lo más viable en ese sentido sería convertirla a Kotlin Multiplatform que le puede dar compatibilidad con Windows, pero mantendría la implicación de reescribir la aplicación parcialmente o en gran parte para adaptarla.

Por otra parte, el concepto 2 puede ser el más práctico si se tiene un programa modular fácil de modificar. En este sentido, es donde entra Scratch. Scratch es código abierto, utiliza módulos llamados “extensiones” para agregar funcionalidades al ambiente de programación, es multiplataforma, es decir, ya es compatible para controlar robots mediante BLE y utilizado en las escuelas del país, por lo, que profesores y estudiantes ya saben utilizarlo. Además, el laboratorio tiene intereses internos de utilizar Scratch para la enseñanza de la robótica y se comentó que la aplicación Android se desarrolló, debido a que en su momento se determinó que no era viable realizar el control por BLE del robot desde Scratch. Sin embargo, proyectos como el TRUETRUEBOT [16] demuestran que la utilización de Web Bluetooth (Base del Scratch Link para comunicación con robots LEGO) con extensiones personalizadas es viable.

En este caso, la estructura de Scratch se encarga de todos los subproblemas excepto de exportar y abrir un archivo que sea compatible con la aplicación Android. Para esto se propone utilizar el string mismo de instrucciones que se le genera al robot, para que al leerlo en la aplicación android o un proyecto de Scratch, se genere la secuencia de bloques respectivos a cada comando.

## 3.5 Pruebas de validación

A continuación, en la tabla 3.16 se presenta una tabla de referencia entre las pruebas de validación y al número de métrica que responden.

38 3.5 Pruebas de validación

Tabla 3.16: Asociación entre pruebas y las métricas a las que responden.

Prueba | Métrica
Compatibilidad actual | 1, 2, 3
Funcionalidad de la expansión lógica de condicionales con base en los sensores infrarrojos | 4,5
Aptitud al uso escolar | 6, 7, 8, 9, 10, 11, 12, 13, 14, 15, 16, 17, 18, 19
Estabilidad por centro de masa | 20
Control por comandos del set de herramientas | 21
Simulación de algoritmos en Scratch | 23,24
Transmisión de comandos desde Scratch | 22
Intercompatibilidad entre plataformas | 25, 26

### 3.5.1 Compatibilidad actual

El propósito de esta prueba es confirmar que los cambios realizados a la programación del microcontrolador del robot no interfiere con la funcionalidad actual de la aplicación y los comandos. Así como, confirmar que el código desarrollado utiliza de base el código previo y el formato de estandarización del laboratorio.

La prueba consiste en ejecutar cada una de los comandos actuales de “For”, movimiento, rotación, herramienta, evasión de caídas y obstáculos desde la aplicación de control Android 5 veces. Se anota si es un éxito o fallo. Junto a una revisión visual de la conformidad del código con la estádarización y la base previa.

### 3.5.2 Funcionalidad de la expansión lógica de condicionales con base en los sensores infrarrojos

El propósito de esta prueba es confirmar que los comandos de “While” e “If” se ejecutan apropiadamente con base en las lecturas de los sensores infrarrojos del robot. Para esto se propone implementar un secuencia de seguidor de línea con ciclos “While” para avanzar hasta el final y condicionales “If” para rotar y mantenerse en curso. La línea se marca con tape negro sobre un fondo blanco de cartulina o cartón y se realiza un arco con una línea transversal al final extremo. Se realizan 30 ensayos, donde se documenta el resultado de

3 Metodología | 39

éxito, sin salirse de la línea o no detenerse al final.

### 3.5.3 Aptitud al uso escolar

El propósito de esta prueba es determinar si la robustez mecánica del ensamble es la adecuada para el ambiente de uso escolar. Además, se aprovecha la ejecución de la prueba para el conteo de equipo, acciones y piezas para realizar el ensamblado; su intercambio, mantenimiento, documentación de su disponibilidad y costo; así como guardado y conformidad con la guía del CPSC.

La prueba consiste en armar los mecanismos en el robot y dejar caer el robot “de cabeza” desde 90 cm de altura. De la prueba se anota si fue un éxito (el ensamble se mantiene completo), desensamble de pieza y cuál pieza (de la caída alguna pieza se separa, pero no se quiebra) o quiebre de pieza y de cuál pieza.

Idealmente de este prueba, en todos los 30 ensayos el ensamble se mantiene completo, pero si se separan piezas sin quebrarse también es aceptable. Las piezas que se quiebren serán revisadas para mejorar su resistencia o rediseñar para que se separen, en vez de quebrarse.

### 3.5.4 Estabilidad por centro de masa

El propósito de esta prueba es determinar si los respectivos diseños de “garra” y “grúa” ensamblados en el robot durante operación desplazan el centro de masa hasta un punto de vuelco. Para eso, se propone armar los respectivos módulos en el robot y levantar las respectivas cargas de las actividades y luego, realizar una secuencia desplazarse 30 cm, una rotación de 360◦y luego, un desplazamiento de -30 cm. Se realizan 30 ensayos y se anota si logra completar la secuencia o si falla, el cómo y durante cuál operación resulta en fallo.

### 3.5.5 Control por comandos del set de herramientas

El propósito es determinar si los respectivos comandos de control activan las herramientas del set apropiadamente. Para esto se realizan 5 ensayos de cada comando, donde se escribe directamente los string de instrucción y se anota si ejecuta la acción de la herramienta.

### 3.5.6 Simulación de algoritmos en Scratch

El propósito de esta prueba es determinar si los algoritmos son simulados apropiadamente en el escenario de Scratch. Para esto se ejecuta cada comando de movimiento, rotación, herramienta y condicional 5 veces y se anota el estado de éxito o fallo. Luego se realiza un algoritmo que incluya todos los comandos y se ejecuta 5 veces. Finalmente, se anota el estado de éxito o fallo.

40 3.5 Pruebas de validación

### 3.5.7 Transmisión de comandos desde Scratch

El propósito de esta prueba es determinar si los string de instrucciones se transmiten correctamente al robot, para esto una secuencia de desplazarse 50 cm, una rotación de 360◦y luego, un desplazamiento de -50 cm se transmite 5 veces y se anota si el robot la ejecuta.

### 3.5.8 Intercompatibilidad entre plataformas

El propósito de esta prueba es determinar si la plataforma Android y la Windows son capaces de exportarse las secuencias del robot. Para esto se realizan cinco secuencias de movimiento, rotación, activación de evasión, activación de herramienta y ciclo for en la plataforma Windows y se importan y exportan los archivos de guardado en formato de la aplicación Android. Además, se anota si el resultado es un éxito o fracaso y se aprovecha la prueba para validar el uso de la arquitectura de Scratch en el desarrollo de la plataforma Windows

# Capítulo 4

# Desarrollo de la expansión del AttaBot-STEM

## 4.1 Proceso de solución

Para darle solución a las problemáticas identificadas en el proyecto, se plantea:

1. Expandir el set de instrucciones soportado por el robot, esto permitiría la implementación de algoritmos más complejos de comportamiento, lo cual expande el tiempo efectivo del robot en el tiempo lectivo, por lo que, se da un aumento del valor agregado de la implementación del proyecto en las aulas. sin aumentar su costo monetario de implementación.
2. Expandir el set de herramientas de interacción con el ambiente, esto aumentaría la variedad y complejidad de las actividades que puede realizar el robot, lo cual abre las puertas a más actividades didácticas en las aulas y aumenta el atractivo del proyecto para ser implementado.
3. Controlar el robot desde Windows, esto es una necesidad y a la vez una ventaja, ya que los laboratorios de informática presentes en escuelas y colegios públicos del país suelen utilizar este sistema operativo en laptops con la disponibilidad de Bluetooth, por lo que, reduciría el costo de implementación del proyecto, al no requerir la disponibilidad o distribución de dispositivos Android junto al robot.

De lo anterior, a continuación se muestra un diagrama del proceso planteado para ejecutar la solución en la fig.4.1:

41

42 4.2 Desarrollo de la solución del set de herramientas

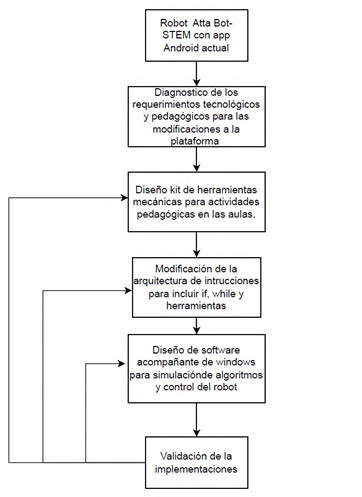
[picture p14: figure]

Figura 4.1: Diagrama del proceso de solución propuesto

## 4.2 Desarrollo de la solución del set de herramientas

De la metodología se obtiene el concepto solución de un servomotor 360 alimentado por la conexión a la Ideaboard y módulos de piezas que permitan ensamblar e intercambiar los mecanismos para interacción del robot AttaBot-STEM.

En general, en el diseño de los mecanismos se utilizan agujeros y ejes nominales de 3 mm. Para compensar por la impresión 3D, los ejes son de 0.2 mm de menor diámetro en el CAD y los agujeros son 0.2 mm mayores en el CAD. Al ensamblar elementos para que roten junto el eje, se utilizan crucetas de 5x2 mm nominales para distribuir la carga y evitar fallas por separación de capas.

Por requisito del proyecto, los mecanismos implementados en el robot necesitan alguna actividad pedagógica para justificar su inclusión. Para esto, se investigó en documentación del MEP sobre los programas de robótica y educación tecnológica, así como por medio de consultas a profesores del área para determinar cuáles actividades ejecutan o podrían ejecutar en clases.

De las actividades recopiladas, se rescatan las de transporte y recolección. La primera actividad es recolectar objetos de distintas geometrías y colores (el cubo rojo, pirámide amarilla, etc.) para crear retos donde el estudiante controle el robot y deba evitar una categoría de elementos, mientras deba recolectar otra categoría. (Por ejemplo: Recolectar solo los cubos rojos.) Para esto se propone el mecanismo de una garra horizontal, para que

4 Desarrollo de la expansión del AttaBot-STEM | 43

el robot arrastre el respectivo elemento.

De segunda actividad se tiene el colocar conceptos en cartas y que el estudiante deba recoger las cartas que responden a una pregunta. Por ejemplo, en cartas tener partes de la computadora y pedirle que recoja las partes que corresponden a las entradas de usuario. Para esta actividad se propone el mecanismo de una grúa vertical que permita tomar la carta y traerla al punto de partida.
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

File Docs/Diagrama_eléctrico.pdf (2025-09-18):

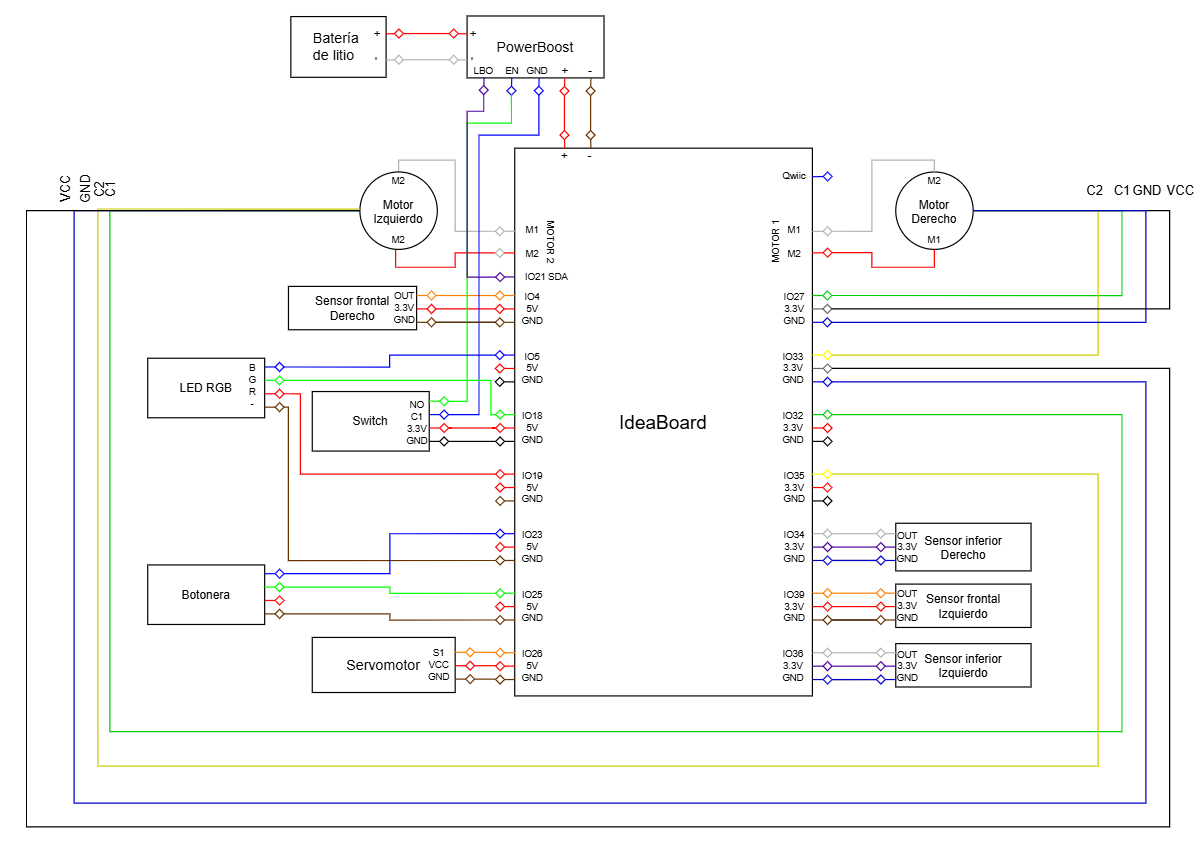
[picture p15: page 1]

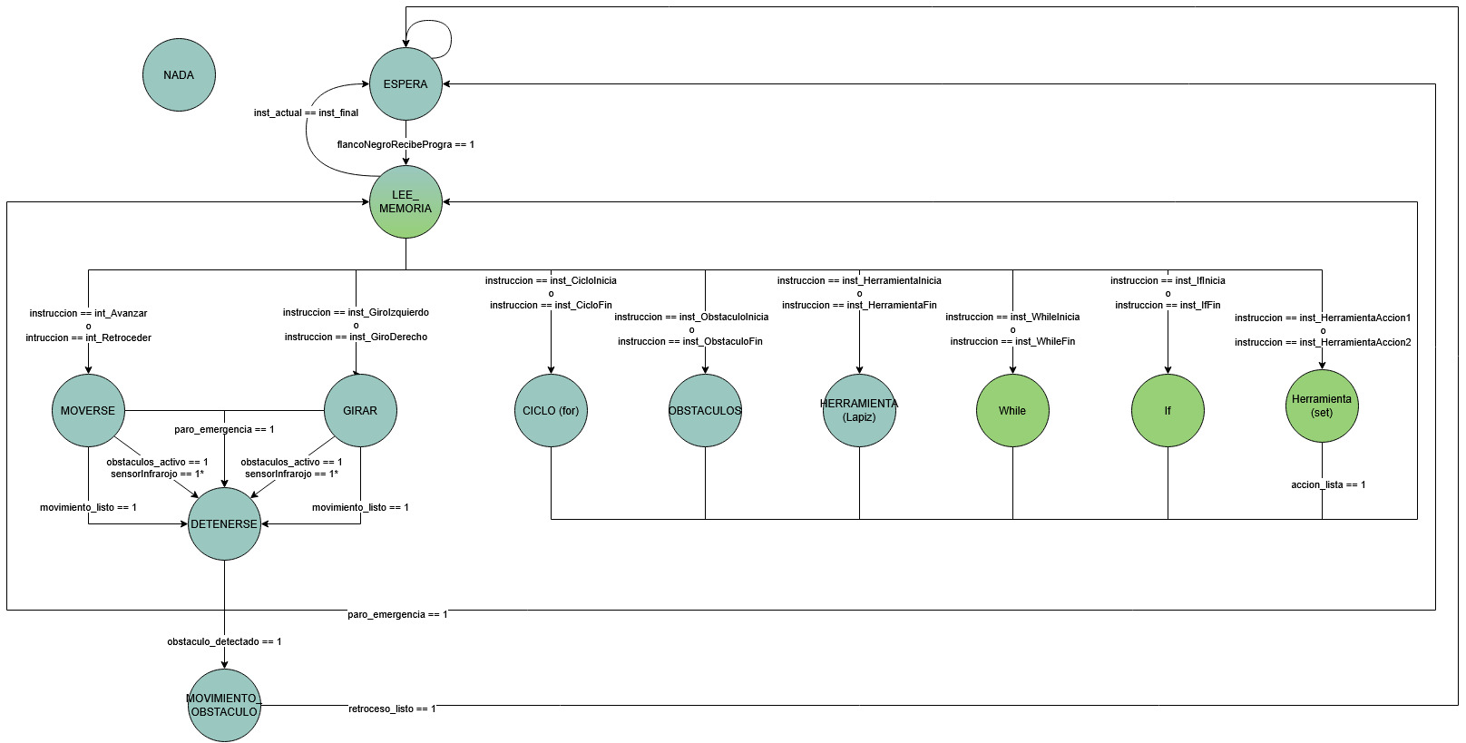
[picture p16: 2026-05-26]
Docs/DiagramasFlujoConceptosEstados.jpg

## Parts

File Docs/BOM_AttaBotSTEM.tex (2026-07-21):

\documentclass[12pt,a4paper]{article}
\usepackage[utf8]{inputenc}
\usepackage[spanish]{babel}
\usepackage{geometry}
\geometry{a4paper, margin=1.8cm}
\usepackage{booktabs}
\usepackage{tabularx}
\usepackage{hyperref}
\usepackage{xcolor}
\usepackage{float}

\hypersetup{
    colorlinks=true,
    linkcolor=blue,
    filecolor=magenta,      
    urlcolor=blue,
    pdftitle={BOM},
}

\title{\textbf{Bill of Materials (BOM)
y Costos de Prototipado}}
\author{AttaBot STEM}
\date{\today}

\begin{document}

\maketitle

Se presenta a continuación la lista de materiales de la versión del robot AttaBotStem más reciente: 

\begin{table}[H]
    \centering
    \renewcommand{\arraystretch}{1.2}
    \begin{threeparttable}
    \begin{tabularx}{\textwidth}{@{} l c l X c @{}}
        \toprule
        \textbf{Nombre} & \textbf{Cant.} & \textbf{Nº de Parte} & \textbf{Enlace} & \textbf{Costo Unit.} \\
        \midrule
        Motor DC con encoder & 2 & ROB-CB0N20 & \href{https://www.crcibernetica.com/n20-gearmotor-with-encoder-and-wheel/}{Referencia} & \$14.95 \\
        Batería Lipo 3.7V 2500mAh & 1 & ADA-328 & \href{https://www.crcibernetica.com/lithium-ion-polymer-battery-3-7v-2500mah/}{Referencia} & \$17.95 \\
        Boost Battery Manager 1000C & 1 & ADA-2465 & \href{https://www.crcibernetica.com/powerboost-1000-charger-rechargeable-5v-lipo-usb-boost-1a-1000c/}{Referencia} & \$32.95 \\
        Soporte Motor Micro & 2 & ROB-CB02443 & \href{https://www.crcibernetica.com/micro-gearmotor-support-bracket/}{Referencia} & \$0.75 \\
        3pi N20 Ball Caster & 1 & ROB-CB1818 & \href{https://www.crcibernetica.com/3pi-n20-ball-caster/}{Referencia} & \$2.75 \\
        IdeaBoard & 1 & ROB-CBIB01 & \href{https://www.crcibernetica.com/crcibernetica-ideaboard/}{Referencia} & \$39.95 \\
        Servomotor MG90S & 1 & MG90S & \href{https://www.crcibernetica.com/mg90s-micro-servo-with-metal-gears/}{Referencia} & \$6.95 \\
        Sensor Infrarrojo delantero & 2 & SEN-CB0006 & \href{https://www.crcibernetica.com/infrared-obstacle-avoidance-module/}{Referencia} & \$2.95 \\
        Sensor Infrarrojo track & 2 & SEN-CB0005 & \href{https://www.crcibernetica.com/track-sensor-module/}{Referencia} & \$1.95 \\
        Kit conectores Dupont & 1 & KIT-CB0012 & \href{https://www.crcibernetica.com/dupont-connector-assorted-kit/}{Referencia} & \$8.95 \textbf{*} \\
        Kit espaciadores Nylon M3 & 1 & TOL-CB0513 & \href{https://www.crcibernetica.com/m3-nylon-screw-black-hex-screw-nut-nylon-pcb-standoff-assortment-kit-250pcs/}{Referencia} & \$15.95 \textbf{*}\\
        Ribbon Cable (6-wire) & 1 & CAB-10646 & \href{https://www.crcibernetica.com/ribbon-cable-6-wire-15ft/}{Referencia} & \$4.50 \textbf{*} \\
        \bottomrule
    \end{tabularx}
    \begin{tablenotes}
        \footnotesize
        \item \textbf{*} son paquetes; con una unidad de cada producto se pueden armar 15 robots completos.} %
    \end{tablenotes}
    \end{threeparttable}
    \caption{Lista de materiales referente a la tienda costarricense CR Cibernética.}
\end{table}

Asimismo, se detallan los costos estimados de impresión y cortes de acrílico para el prototipo:

\begin{table}[H]
    \centering
    \renewcommand{\arraystretch}{1.2}
    \begin{tabularx}{\textwidth}{@{} l c X c @{}}
        \toprule
        \textbf{Descripción} & \textbf{Material} & \textbf{Detalles} & \textbf{Costo Est. (\$)} \\
        \midrule
        Cortes Láser & Acrílico & Costo por minuto & En espera \\
        Impresión 3D & PLA / ABS & ₡50 por gramo (120g) & 13.21 \\
        \bottomrule
    \end{tabularx}
    \caption{Estimación de costos de manufactura para el prototipo según precios de Impresión y Corte en Laboratorio LAIMI-TEC Sede Cartago.}
\end{table}

Con la información anterior se puede estimar que el prototipo completo tiene un precio total de \$184.41 (aproximadamente ₡83\,765). Cabe destacar que ciertos componentes, como los kits de espaciadores, conectores Dupont y cable Ribbon no son vendidos por separado, y adquirir uno de estos da abasto para armar hasta 15 prototipos completos, lo cual reduce el costo unitario a \$156.92 (aproximadamente ₡70\,890).

\end{document}

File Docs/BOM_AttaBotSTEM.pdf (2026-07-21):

# Bill of Materials (BOM) y Costos de Prototipado

### AttaBot STEM

### 21 de julio de 2026

Se presenta a continuaci´on la lista de materiales de la versi´on del robot AttaBotStem m´as reciente:

Nombre | Cant. Nº de Parte | Enlace | Costo Unit.
Motor DC con encoder | 2 | ROB-CB0N20 | Referencia (https://www.crcibernetica.com/n20-gearmotor-with-encoder-and-wheel/) | $14.95
Bater´ıa Lipo 3.7V 2500mAh | 1 | ADA-328 | Referencia (https://www.crcibernetica.com/lithium-ion-polymer-battery-3-7v-2500mah/) | $17.95
Boost Battery Manager 1000C | 1 | ADA-2465 | Referencia (https://www.crcibernetica.com/powerboost-1000-charger-rechargeable-5v-lipo-usb-boost-1a-1000c/) | $32.95
Soporte Motor Micro | 2 | ROB-CB02443 Referencia (https://www.crcibernetica.com/micro-gearmotor-support-bracket/) | $0.75
3pi N20 Ball Caster | 1 | ROB-CB1818 | Referencia (https://www.crcibernetica.com/3pi-n20-ball-caster/) | $2.75
IdeaBoard | 1 | ROB-CBIB01 | Referencia (https://www.crcibernetica.com/crcibernetica-ideaboard/) | $39.95
Servomotor MG90S | 1 | MG90S | Referencia (https://www.crcibernetica.com/mg90s-micro-servo-with-metal-gears/) | $6.95
Sensor Infrarrojo delantero | 2 | SEN-CB0006 | Referencia (https://www.crcibernetica.com/infrared-obstacle-avoidance-module/) | $2.95
Sensor Infrarrojo track | 2 | SEN-CB0005 | Referencia (https://www.crcibernetica.com/track-sensor-module/) | $1.95
Kit conectores Dupont | 1 | KIT-CB0012 | Referencia (https://www.crcibernetica.com/dupont-connector-assorted-kit/) | $8.95 *
Kit espaciadores Nylon M3 | 1 | TOL-CB0513 | Referencia (https://www.crcibernetica.com/m3-nylon-screw-black-hex-screw-nut-nylon-pcb-standoff-assortment-kit-250pcs/) | $15.95 *
Ribbon Cable (6-wire) | 1 | CAB-10646 | Referencia (https://www.crcibernetica.com/ribbon-cable-6-wire-15ft/) | $4.50 *

* son paquetes; con una unidad de cada producto se pueden armar 15 robots completos.

Cuadro 1: Lista de materiales referente a la tienda costarricense CR Cibern´etica.

Asimismo, se detallan los costos estimados de impresi´on y cortes de acr´ılico para el prototipo:

Descripci´on | Material | Detalles | Costo Est. ($)
Cortes L´aser | Acr´ılico | Costo por minuto | En espera
Impresi´on 3D PLA / ABS ₡50 por gramo (120g) | 13.21

Cuadro 2: Estimaci´on de costos de manufactura para el prototipo seg´un precios de Impresi´on y Corte en Laboratorio LAIMI-TEC Sede Cartago.

Con la informaci´on anterior se puede estimar que el prototipo completo tiene un precio total de $184.41 (aproximadamente ₡83 765). Cabe destacar que ciertos componentes, como los kits de espaciadores, conectores Dupont y cable Ribbon no son vendidos por separado, y adquirir uno de estos da abasto para armar hasta 15 prototipos completos, lo cual reduce el costo unitario a $156.92 (aproximadamente ₡70 890).

| | 1

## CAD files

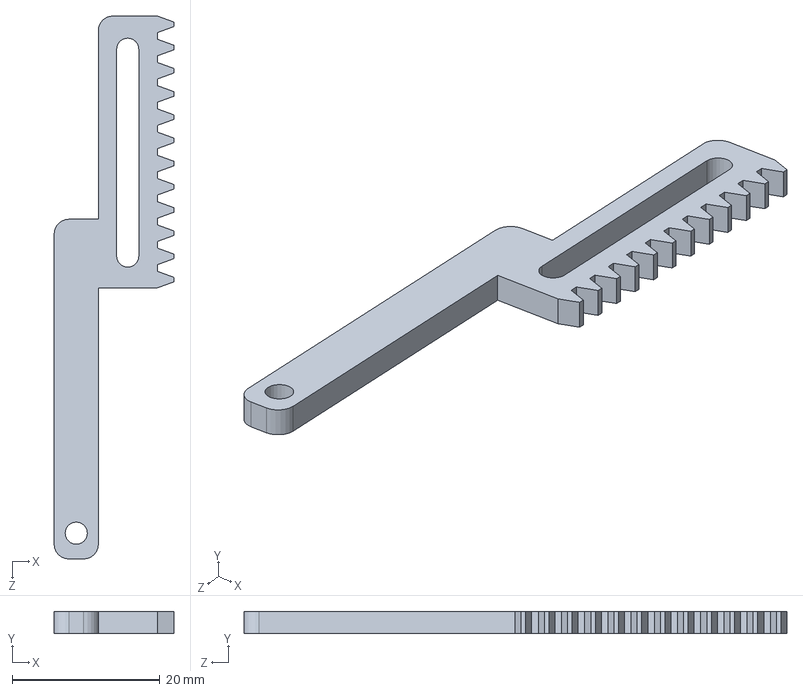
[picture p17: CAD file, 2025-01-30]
Chasis/3. Diseños Anteriores/Pieza_de_cremallera_Lapicero_FULL.SLDPRT
16.2 x 3.00 x 73.5 mm

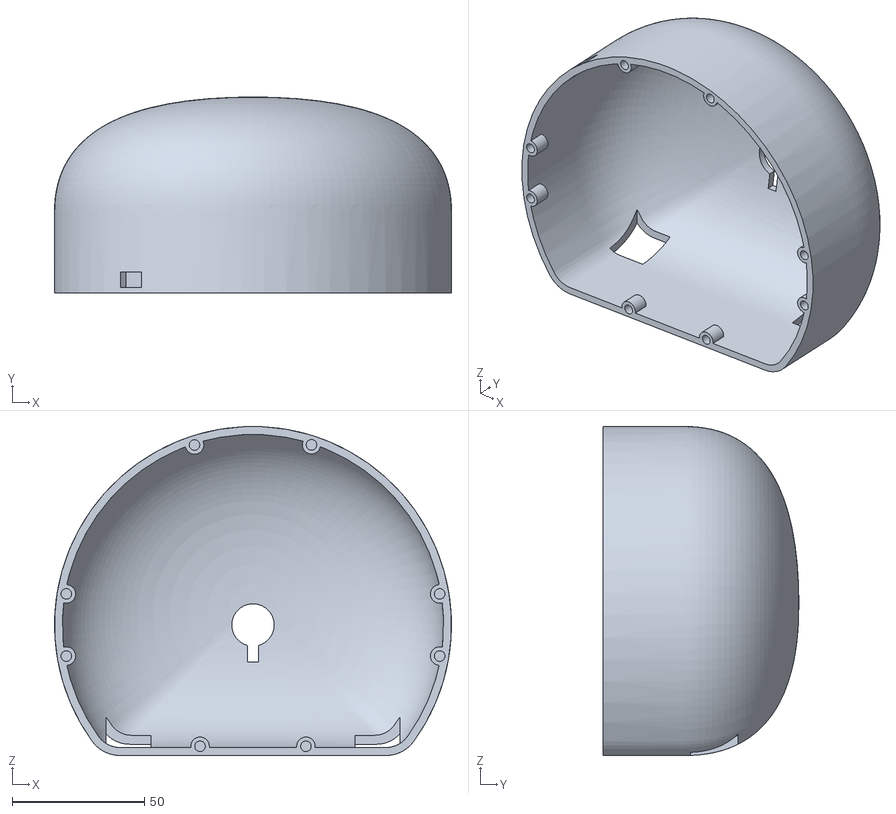
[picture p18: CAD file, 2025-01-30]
Chasis/3. Diseños Anteriores/STL_DSK_PLANOS_CORTE/Prueba_chasis_Full.STL
150.0 x 74.0 x 124.3

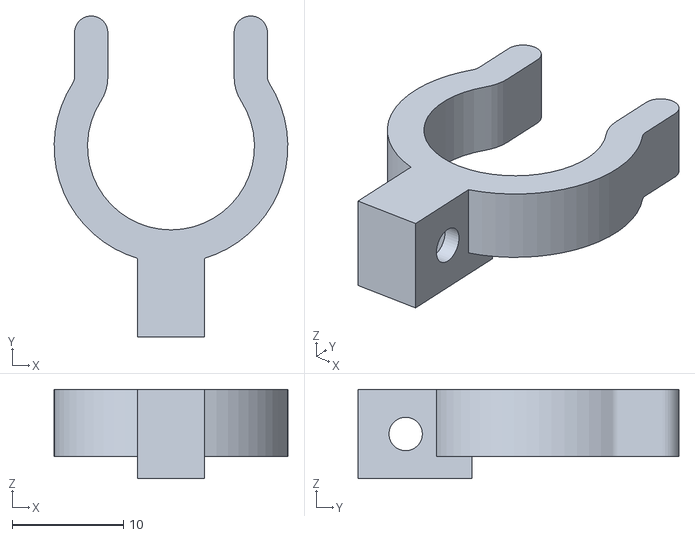
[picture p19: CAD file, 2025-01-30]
Chasis/3. Diseños Anteriores/STL_DSK_PLANOS_CORTE/Sujetador_De_Marcador_2Largo_FULL.STL
21.0 x 28.8 x 8.00

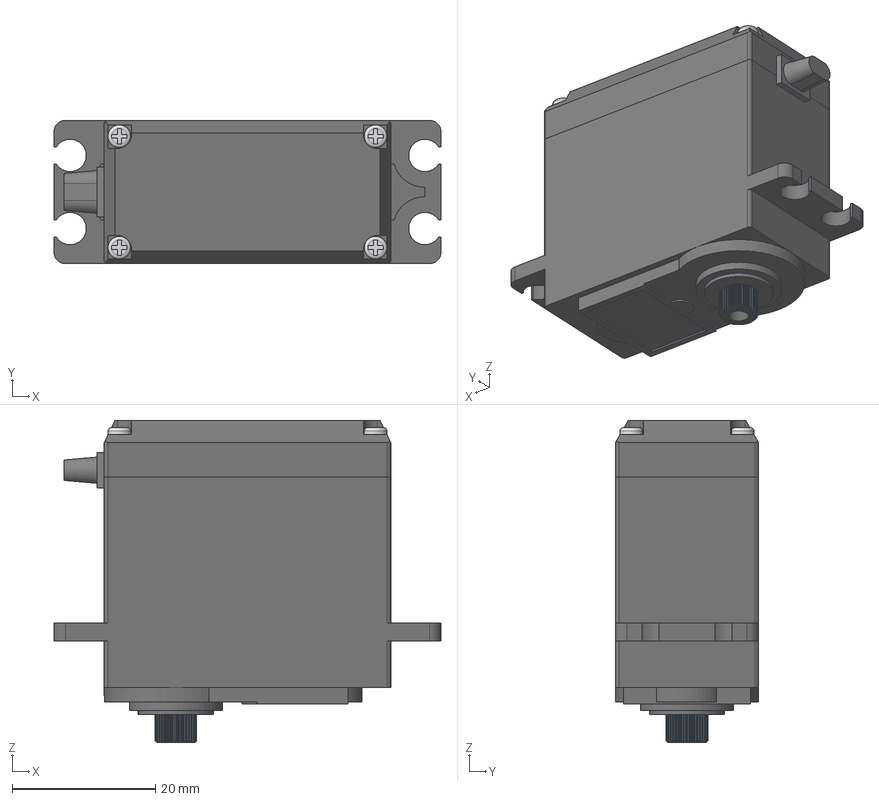
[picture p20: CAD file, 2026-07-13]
Chasis/1. Diseño V3.0/SetHerramientas/Elementos/mg995-servo-motor-metal-gear-high-torque-standard-size-1.snapshot.1/MG995.step
54.0 x 20.0 x 45.0 mm

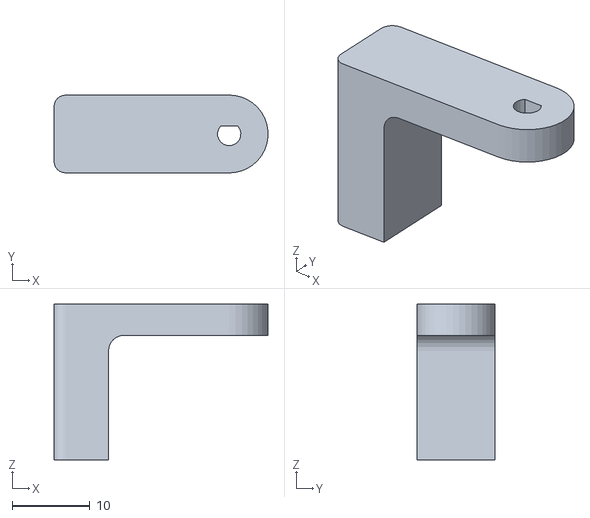
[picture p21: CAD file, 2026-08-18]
Chasis/2. Archivos Para Impresión/STL/AcoplePPR.stl
27.5 x 10.0 x 20.0

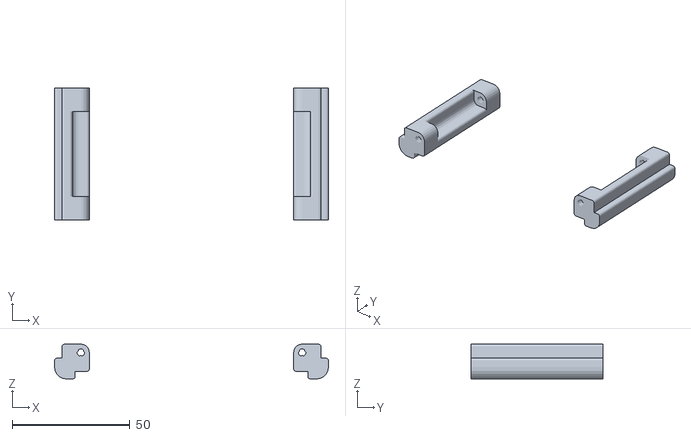
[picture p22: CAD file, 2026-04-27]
Chasis/2. Archivos Para Impresión/STL/Esquineros Delanteros.stl
116.4 x 56.0 x 14.8

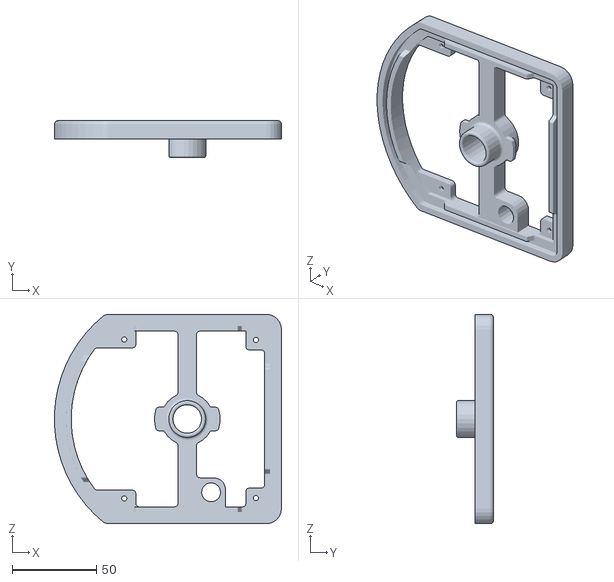
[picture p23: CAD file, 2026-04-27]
Chasis/2. Archivos Para Impresión/STL/Techo Armadura.stl
134.9 x 22.0 x 124.4

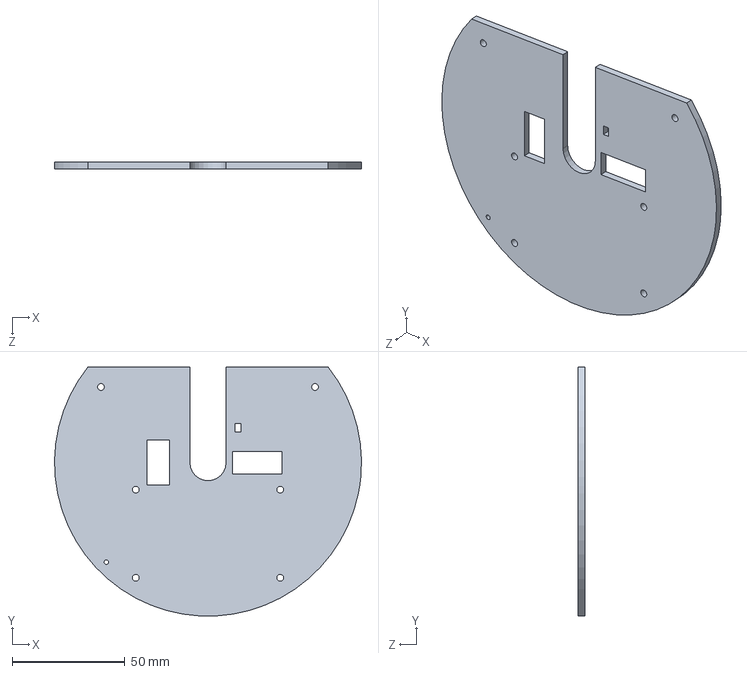
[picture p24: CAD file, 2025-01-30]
Chasis/3. Diseños Anteriores/Nivel_interno_V2.SLDPRT
136.0 x 110.2 x 3.00 mm

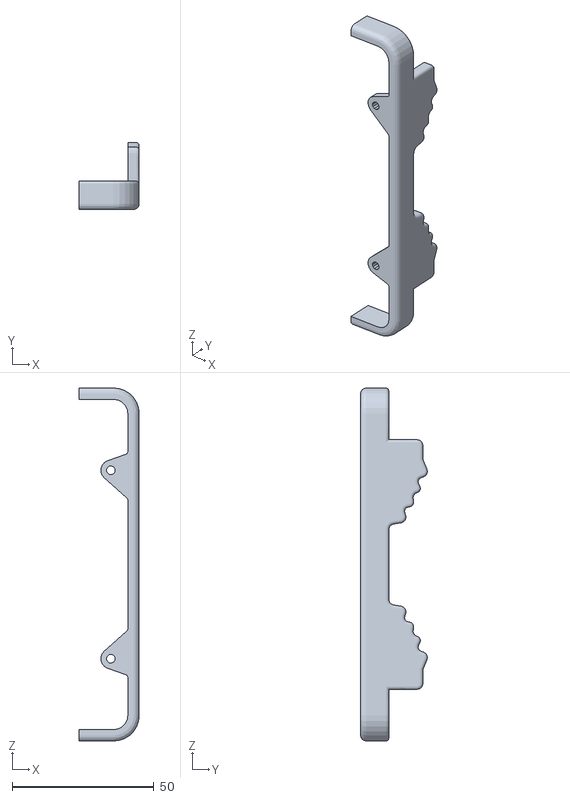
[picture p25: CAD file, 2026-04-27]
Chasis/2. Archivos Para Impresión/STL/Bumper Delantero.stl
21.3 x 23.6 x 124.4

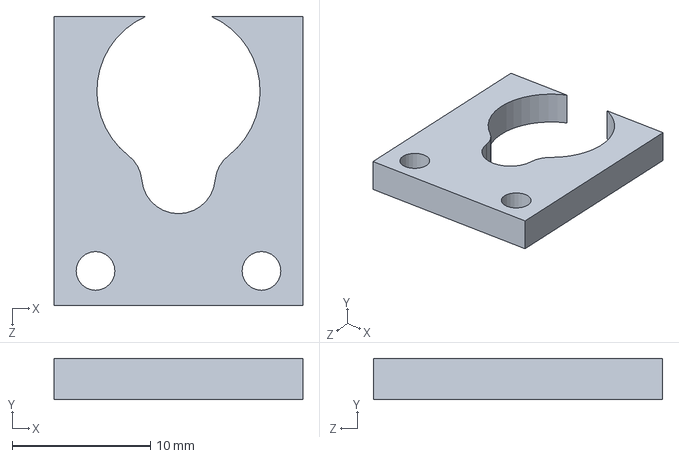
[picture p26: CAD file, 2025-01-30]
Chasis/3. Diseños Anteriores/Pieza_SujecionMotorLift_5_final_si.SLDPRT
18.0 x 3.00 x 20.9 mm

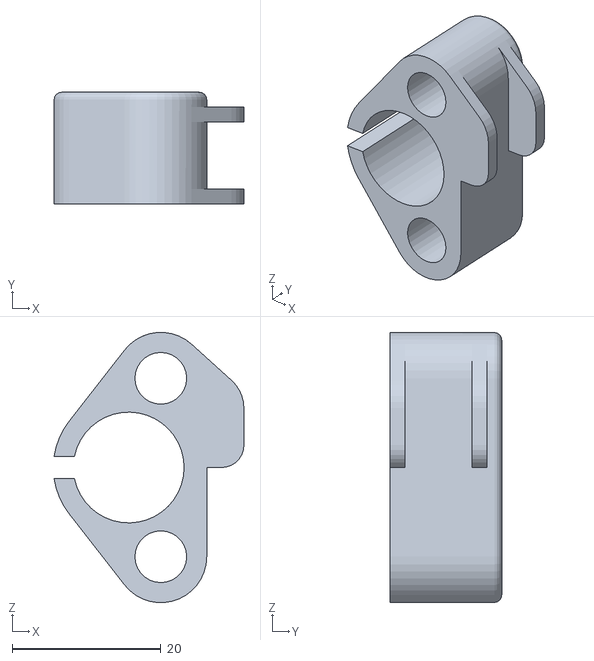
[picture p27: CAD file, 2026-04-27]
Chasis/2. Archivos Para Impresión/STL/PrensaPilotInventorVersion.stl
25.5 x 15.0 x 36.3

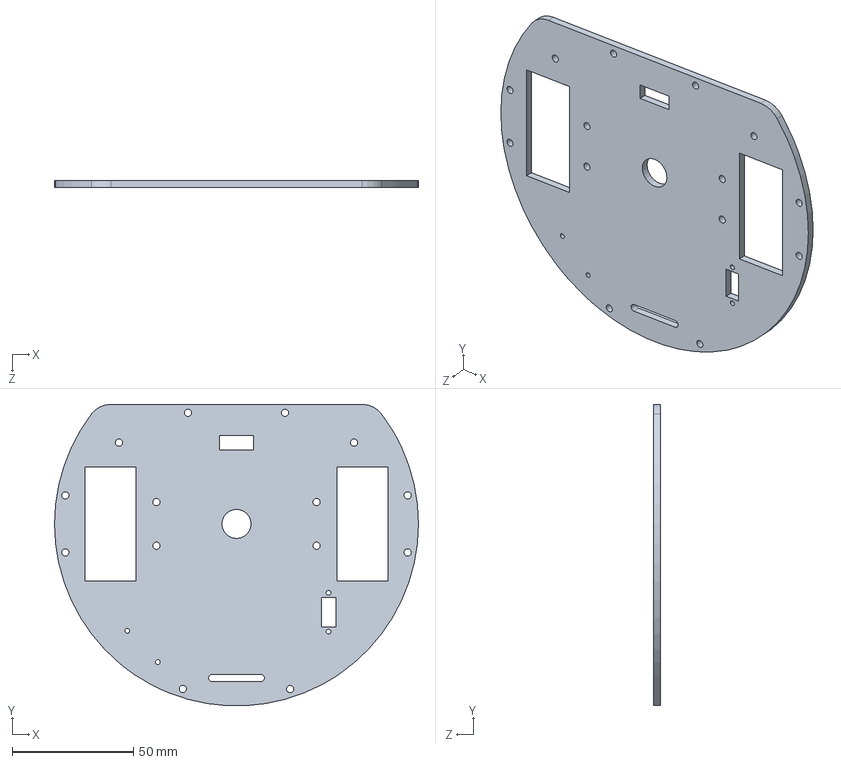
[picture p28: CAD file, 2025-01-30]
Chasis/3. Diseños Anteriores/Base_Chasis_V3.SLDPRT
150.0 x 124.2 x 3.00 mm

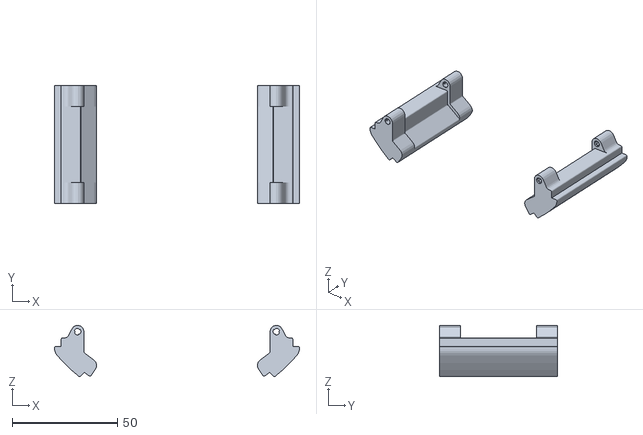
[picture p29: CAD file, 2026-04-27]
Chasis/2. Archivos Para Impresión/STL/Esquinero Trasero.stl
116.4 x 56.0 x 24.4

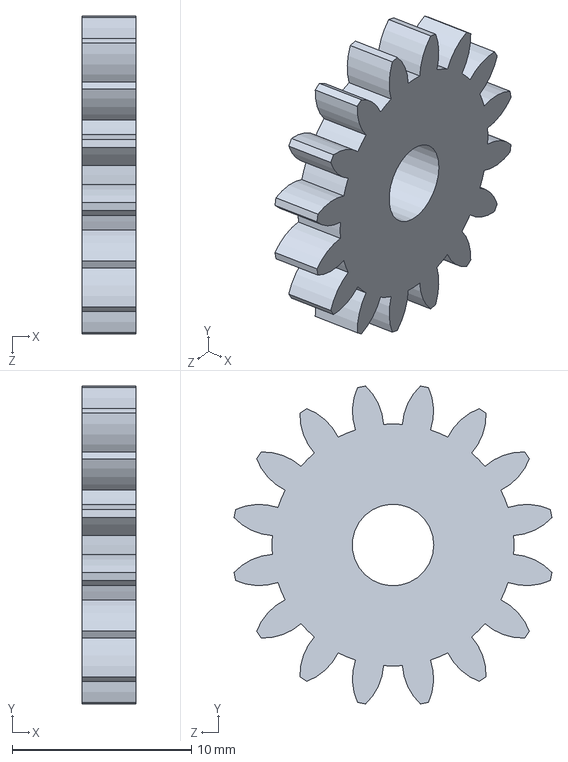
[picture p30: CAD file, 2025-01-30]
Chasis/3. Diseños Anteriores/Pieza_EngraneLift_2.SLDPRT
3.00 x 17.7 x 17.7 mm

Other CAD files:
Chasis/3. Diseños Anteriores/Prueba_chasis_FULL.SLDPRT
Chasis/3. Diseños Anteriores/Sujetador_De_Marcador_2Largo_FULL.SLDPRT
Chasis/1. Diseño V3.0/AttaBot Stem Acrilics.dwg
Chasis/2. Archivos Para Impresión/STL/Guardabarros.stl
Chasis/1. Diseño V3.0/AcoplePPR.ipt
Chasis/1. Diseño V3.0/Acrilicos Superiores.ipt
Chasis/1. Diseño V3.0/Bumper Delantero.ipt
Chasis/1. Diseño V3.0/Bumper Trasero.ipt
Chasis/1. Diseño V3.0/Content Center Files/en-US/ISO 4032(2)/ISO 4032 - M2 - ISO.ipt
Chasis/1. Diseño V3.0/Content Center Files/en-US/ISO 4032(2)/ISO 4032 - M3 - ISO.ipt
Chasis/1. Diseño V3.0/Content Center Files/en-US/ISO 4032(2)/OldVersions/ISO 4032 - M2 - ISO.0001.ipt
Chasis/1. Diseño V3.0/Content Center Files/en-US/ISO 4032(2)/OldVersions/ISO 4032 - M3 - ISO.0001.ipt
Chasis/1. Diseño V3.0/Content Center Files/en-US/ISO 4762(2)/ISO 4762 - M2 x 12ISO.ipt
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

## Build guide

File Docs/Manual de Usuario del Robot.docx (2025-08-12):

Manual de Usuario del Robot “Atta Bot STEM”

[FOTO]

Nombre de la organización o autores

Fecha:

# Introducción

- Objetivo del Manual: Breve descripción del propósito del manual, que es guiar a los usuarios en el uso, programación, instalación y mantenimiento del robot.
- Descripción General del Robot:
  - Breve introducción sobre el Atta-Bot, destacando su función en educación.
  - Características clave: movilidad, sensores, autonomía, etc.
  - Imagen del robot.

# Descripción Técnica

- Especificaciones Técnicas:
  - Dimensiones: X x Y x Z mm.
  - Peso: W g.
  - Autonomía: >A minutos.
  - Velocidad: B mm/s.
  - Componentes: Detallar los componentes electrónicos, como microcontroladores, sensores (infrarrojos, distancia, temperatura), motores, etc.
  - Diagrama de Arquitectura del Sistema:
    - Mostrar un diagrama general de los subsistemas (como en el diagrama de alto nivel mostrado en el archivo), que puede incluir los subsistemas de movimiento, sensores y controlPFG_Leisel _Villalobos.

# Instrucciones de Uso

- Encendido y Apagado del Robot:
  - Procedimiento para iniciar y apagar el robot de manera segura.
- Modos de Operación:
  - Descripción de los modos disponibles:
    - Avanzar, retroceder, girar, etc.
    - Instrucciones sobre cómo cambiar entre los diferentes modos a través de los controles.
  - Detalle de las funcionalidades adicionales: detección de obstáculos, ciclos de movimiento.
- Interfaz de Usuario:
  - Explicar la interfaz de la aplicación móvil o software que conecta con el robot.
  - Ejemplo de cómo ingresar comandos para controlar el robot (usar instrucciones básicas de código si es necesario).

# Programación

- Programación Básica:
  - Instrucciones sobre cómo programar el robot utilizando el entorno de desarrollo Arduino IDE.
  - Explicación de la máquina de estados y cómo se utilizan las instrucciones (avanzar, girar, detenerse)
- Conexión con la Aplicación:
  - Cómo vincular el robot con la aplicación móvil.
  - Explicación de cómo modificar el comportamiento del robot mediante la interfaz de usuario.

# Mantenimiento y Solución de Problemas

- Mantenimiento Regular:
  - Instrucciones para el mantenimiento de la batería, limpieza de sensores, y verificación del sistema de movimiento.
- Solución de Problemas Comunes:
  - Qué hacer si el robot no responde a los comandos.
  - Resolución de problemas de conexión con la aplicación.
  - Diagnóstico de fallos de los sensores.

# Seguridad

- Precauciones Generales:
  - Uso seguro del robot en ambientes educativos.
  - Cuidado con componentes eléctricos y baterías.
- Manejo de Emergencias:
  - Procedimientos de apagado de emergencia.
  - Indicadores de fallo y cómo proceder.

# Anexos

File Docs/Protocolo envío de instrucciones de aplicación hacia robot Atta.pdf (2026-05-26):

Protocolo envío de instrucciones de aplicación hacia robot Atta-Bot STEM

Versión: 25/Mayo/2026

Consideraciones:

- Cada comando enviado será de 5 caracteres
- No habrá divisiones entre comandos (comas, espacios, etc)
- Se tendrá un comando de encabezado y un comando de finalización al enviar el mensaje completo

Lista de comandos:
Comando | Detalles
ATINI | Encabezado del mensaje con instrucciones
ATFIN | Finalización del mensaje con instrucciones
OBINI | Inicio de la detección de obstáculos
OBFIN | Finalización de la detección de obstáculos
CI### | Inicio del ciclo. Por ### cantidad de repeticiones
CIFIN | Finalización del ciclo
WH### | Inicio del ciclo condicional while. Según ### condición.
WHFIN | Finalización del ciclo condicional while
IF### | Inicio de bifurcación If. Según ### condición.
EL### | Inicio de bifurcación ElseIf. Según ### condición.
IFFIN | Finalización de bifurcación If
AV### | Avanzar una distancia de ### cm
RE### | Retroceder una distancia de ### cm
GI### | Giro a la izquierda un ángulo de ### grados
GD### | Giro a la derecha un ángulo de ### grados
HEINI | Inicio del uso del marcador
HEFIN | Finalización del uso del marcador
HE### | Activación del servomotor del set de herramienta. ### es la acción.
ATCOI | Encabezado del mensaje de control
ATCOF | Finalización del mensaje de control
PARAR | Detener el robot
EJECU | Ejecutar comandos guardados en la memoria del robot

Nota 1: Para todos los comandos con ###, esto representa un número entero de 3 dígitos sin signo.

Nota 2: Todos los comandos relacionados a instrucciones que el robot debe ejecutar en secuencia van con los encabezados de “mensaje con instrucciones”. Los comandos que se deben ejecutar con prioridad sobre cualquier otra tarea van con los encabezados de control.

Nota 3: Para los comandos IF/WH: ### representa las condiciones de los sensores infrarrojos:

IF | No se usa | Sensor traker izquierdo | Sensor traker derecho
000 | | No detecta | No detecta
001 | | No detecta | Detecta
010 | | Detecta | No detecta
011 | | Detecta | Detecta
WHILE/ WhileNot | Mientras/ Hasta | Sensor traker izquierdo | Sensor traker derecho
100 Hasta/ | WhileNot | No detecta | No detecta
000 Mientras/ | While | No detecta | No detecta

Nota 4: Para el comando HE###, esto representa una acción:

101 Abrir Garra
001 Cerrar Garra
102 Subir Grúa
002 Bajar Grúa

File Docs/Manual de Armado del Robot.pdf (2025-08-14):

# Manual de Armado del Robot “Atta Bot STEM”

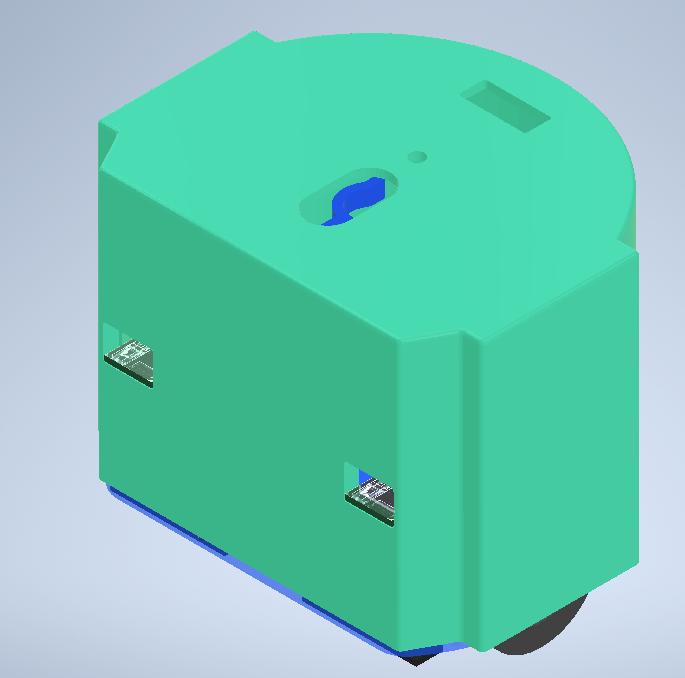
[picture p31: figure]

Grupo de Investigación en Robótica Múltiple, Escuela de Matemática, Tecnológico de Costa Rica

Fecha: 27/07/25

2

Tabla de contenidos

3

Lista de Materiales

Tabla 1. Componentes mecánicos y estructuras de robot

Cantidad | Componente
2 | Soporte Motor
2 | Ruedas
1 | Ball Caster
1 | Cremallera
1 | Base Cremallera
1 | Engrane
1 | Prensa Pilot
1 | Base inferior
1 | Base intermedia
1 | Base superior
1 | Carcasa Robot

4

Tabla 2. Tornillos, espaciadores y kits

Cantidad | Componente
1 | Kit conectores
4 | Tornillos M2 12 mm
7 | Tornillos M2 8 mm
2 | Tornillos M2 6 mm
2 | Tornillos M3 12 mm
8 | Tornillos M3 8 mm
6 | Tornillos M3 6 mm
17 | Tuercas M2
18 | Tuercas M3
1 | Kit espaciadores
4 | Espaciador M3 20+6mm
4 | Espaciador M3 10+6mm
6 | Espaciador M3 6+6mm
1 | Kit Precisión

5

Tabla 3. Componentes electrónicos de robot

Cantidad | Componente
2 | Motor DC con encoder
1 | Batería Lipo 3.7V
1 | Boost Battery Manager
1 | IdeaBoard
1 | Servomotor
2 | Sensor Infrarrojo delantero
2 | Sensor Infrarrojo inferior
1 | Botones
1 | Switch
11 | Jumpers Hembra – Hembra
4 | Jumpers Macho – Hembra
2 | Cable Motor Encoder 6 Pos

6

Bolsa 1: Base inferior

Cantidad | Componente
2 | Motor DC con encoder
2 | Ruedas
2 | Soporte Motor
2 | Cable Motor Encoder 6 Pos
1 | Base de Carrito
1 | Ball Caster (tornillos incluidos)
2 | Sensor Infrarrojo Inferior
1 | Switch
4 | Tornillos M2 8mm
2 | Tornillos M2 6mm
6 | Tuercas M2
2 | Tornillos M3 12 mm
2 | Tornillos M3 8 mm
6 | Tuercas M3
4 | Espaciadores M3 20+6 mm
8 | Espaciadores M3 10+6 mm
6 | Jumpers Hembra-Hembra

7

Bolsa 2: Base Intermedia

Cantidad | Componente
1 | Batería Lipo 3.7V
1 | Powerboost
1 | Base intermedia
2 | Tornillos M2 12 mm
2 | Tornillos M2 8 mm
8 | Tuercas M2
4 | Tornillos M3 8 mm
3 | Jumpers Hembra-Hembra

8

Bolsa 3: Base superior

Cantidad | Componente
1 | Ideaboard
2 | Sensores infrarrojos delanteros
1 | Servomotor
2 | Tornillos M3 8 mm
6 | Tornillos M3 6 mm
6 | Espaciadores M3 6+6mm
12 | Tuercas M3
2 | Tornillo M2 12 mm
1 | Tornillo M2 8 mm
3 | Tuerca M2
1 | Base superior
2 | Soporte Servomotor
1 | Engrane
1 | Cremallera
1 | Base Cremallera
1 | Prensa Pilot
6 | Jumpers Hembra-Hembra

9

Precauciones iniciales

- Es importante tener cuidado con las piezas, ya que muchas pueden ser frágiles.
- Si es menor de 15 años, estar acompañado de un adulto en todo momento.
- Tener precaución a la hora de conectar los circuitos eléctricos y corroborar que todo esté en su lugar.
- No tocar circuitos abiertos ni componentes eléctricos mal conectados.

10

## Pasos de armado Bolsa 1

### 1. Conectar ruedas y ajustar soporte en ambos motores. El eje del motor debe

salirse aproximadamente 1 mm respecto a la parte blanca de la llanta.

Materiales:

- 2X Motores con Encoder
- 2X ruedas
- 2X Soportes motor

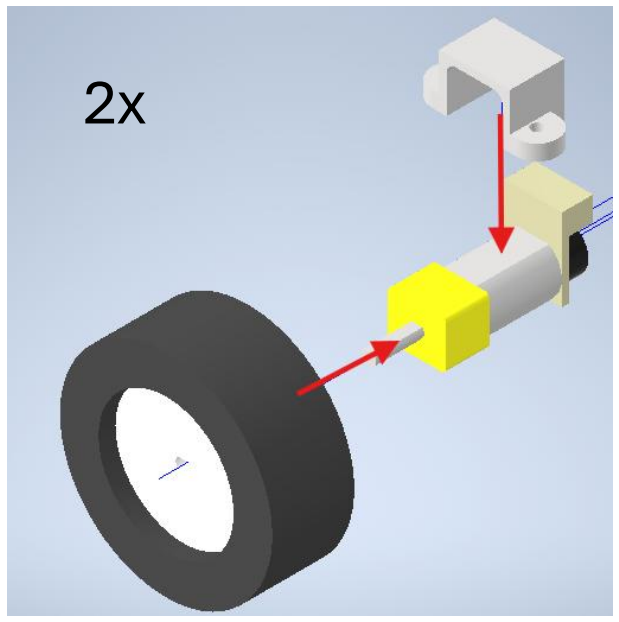
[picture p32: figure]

11

### 2. Conectar motores a la base del carrito con tornillos y tuercas M2. Tener

cuidado con orientación de tornillo, ya que se inserta en orificio y se ajusta desde debajo de la base. (Utilice Kit Precision)

Materiales:

- 1X Base de Carrito
- 4X Tornillos M2 8 mm
- 4X Tuercas M2

2x

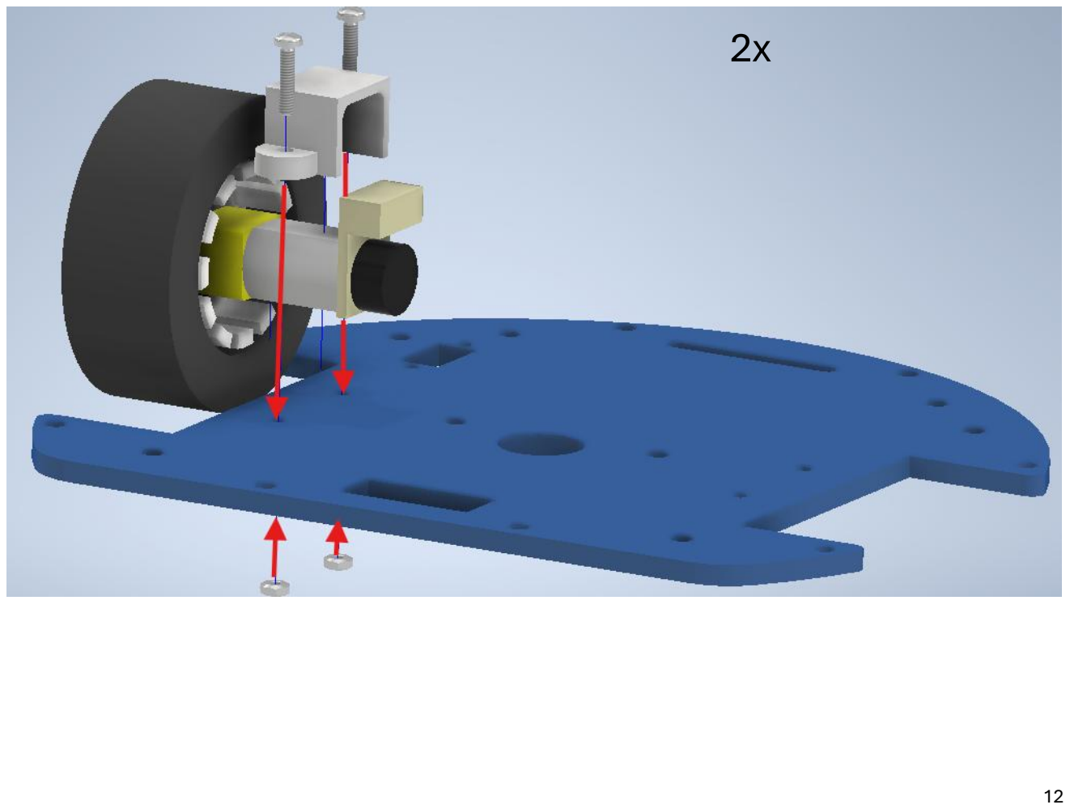
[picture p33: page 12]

12

13

3. Conectar Ball Caster a la base del carrito con tornillos de este componente. (Utilice Kit Precisión)

Materiales:

- 1X Ball Caster (tornillos vienen incluidos con componente)

14

### 4. Conectar Switch a base del carrito utilizando tornillos M2 de 6mm y tuercas

M2. Manualmente inserte el tornillo, enrosque la tuerca, y luego ajuste el tornillo. (Utilice Kit Precision)

Materiales:

- 1X Switch
- 2X Tornillos M2 6mm
- 2X Tuercas M2

15

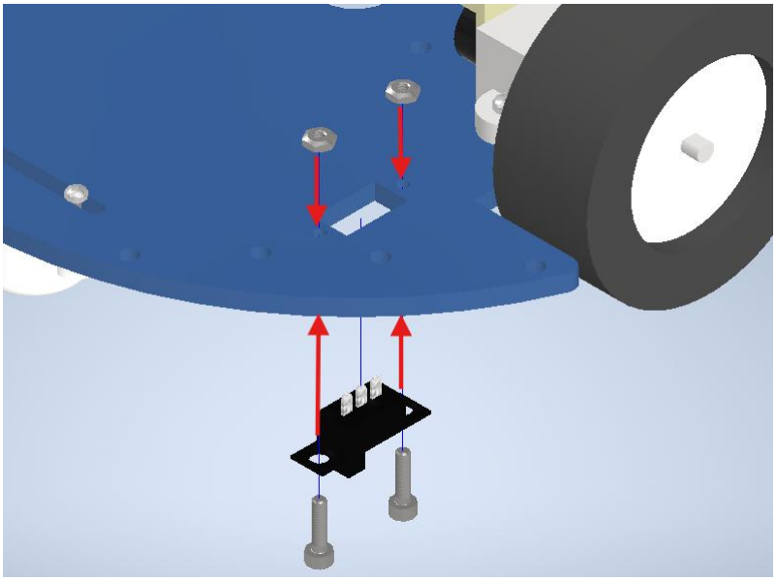
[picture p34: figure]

16

### 5. Conectar Jumpers Hembra-Hembra a sensores infrarrojos inferiores a la base

del carrito.

Materiales:

- 6X Jumpers Hembra-Hembra
- 2X Sensor Infrarrojo Inferior

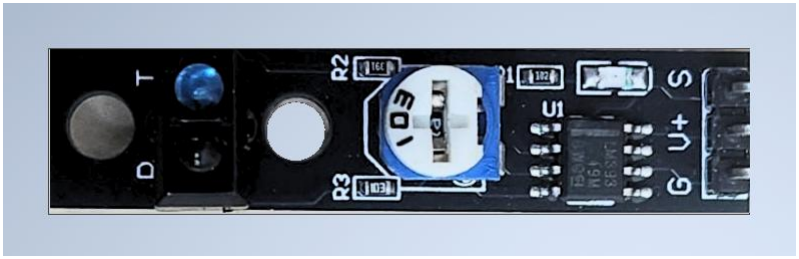
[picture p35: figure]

17

### 6. Conectar sensores infrarrojos inferiores a la parte inferior de la base del carrito

con tornillos M3 12 mm, tuercas M3 y espaciadores M3 20+6 mm. Insertar tornillo en orificio de sensor y ajustar por el otro lado manualmente con el espaciador para conectar componente. (En caso de que la pieza quede floja, ajustar con Kit de Precisión)

Materiales:

- 2X Espaciadores M3 20+6 mm
- 2X Tornillos M3 12 mm
- 2X Tuercas M3

18

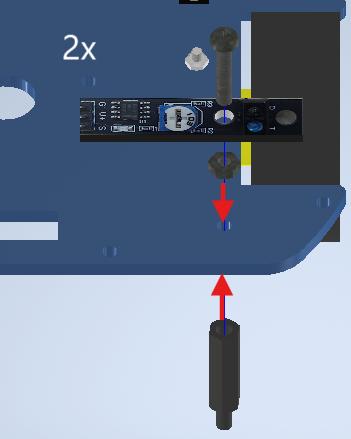
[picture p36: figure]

19

7. Conectar espaciadores M3 10+6 mm encima de espaciadores M3 20+6 mm. Inserte y ajusta manualmente espaciadores.

Materiales:

- 2X Espaciadores M3 10+6 mm

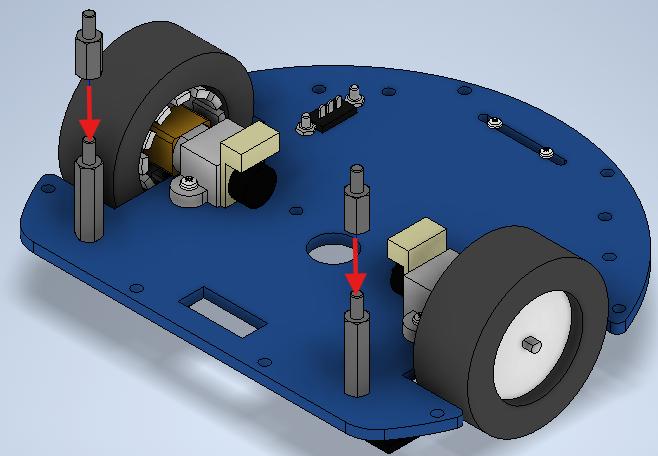
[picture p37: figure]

20

8. Insertar espaciadores M3 20+6 mm y tornillos M3 8 mm en base del carrito. Inserte tornillo en lugar correspondiente por debajo y ajustar manualmente el espaciador.

Materiales:

- 2X Espaciadores M3 20+6 mm
- 2X Tornillos M3 8 mm.

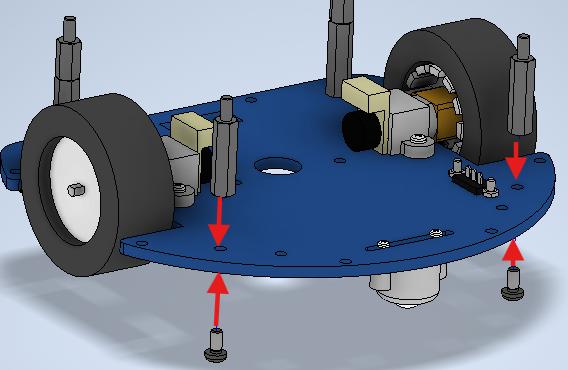
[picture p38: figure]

21

9. Conectar espaciadores M3 10+6 mm encima de espaciadores M3 20+6 mm. Inserte y ajusta manualmente espaciadores.

Materiales:

- 2X Espaciadores M3 10+6 mm

22

### 10. Conectar espaciadores M3 10+6 mm en base del carrito. Ajustar con

tuercas M3 para conectar a la base los espaciadores. (Utilice Kit de Precision)

Materiales:

- 4X Espaciadores M3 10+6 mm
- 4X Tuercas M3

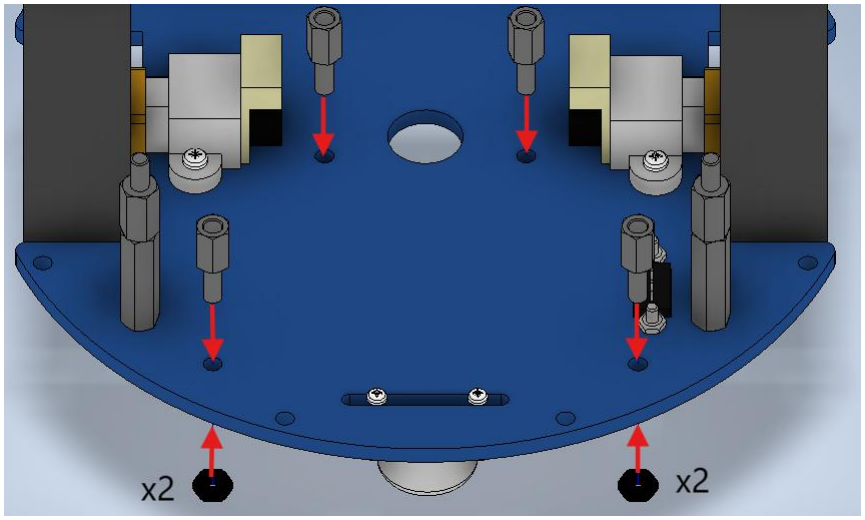
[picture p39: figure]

23

11. Conectar Cable Encoder para motor.

Materiales:

- 2X Cable Motor Encoder 6 Pos

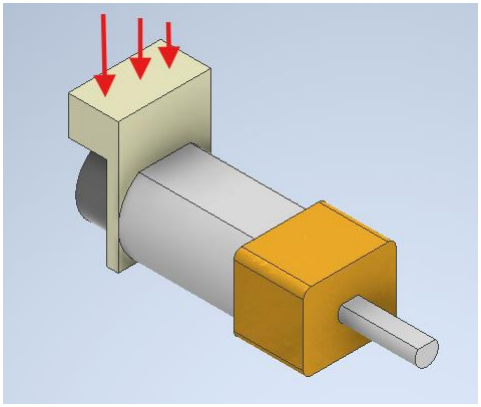
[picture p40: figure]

24

Resultado esperado al terminar la bolsa 1.

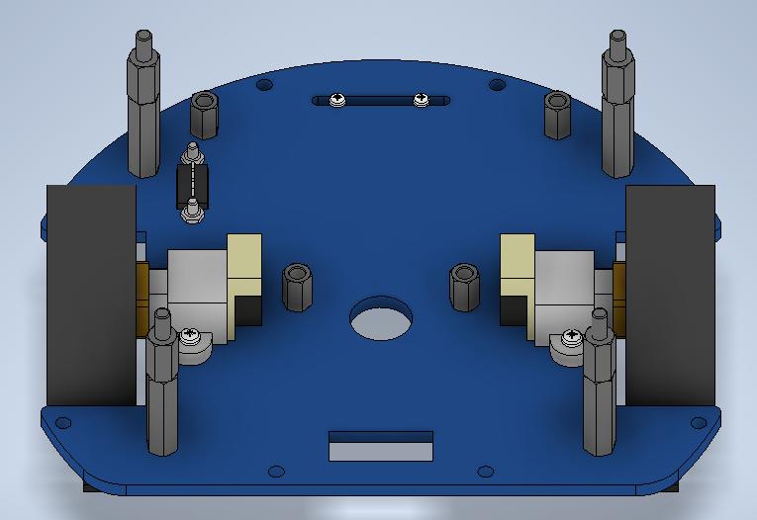
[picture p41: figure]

25

## Pasos de armado Bolsa 2

### 12. Insertar batería en medio de espaciadores en base del carrito. (Observar

orientación de batería y lado para no tener problemas a futuro.

Materiales:

- 1X Batería 3.7V

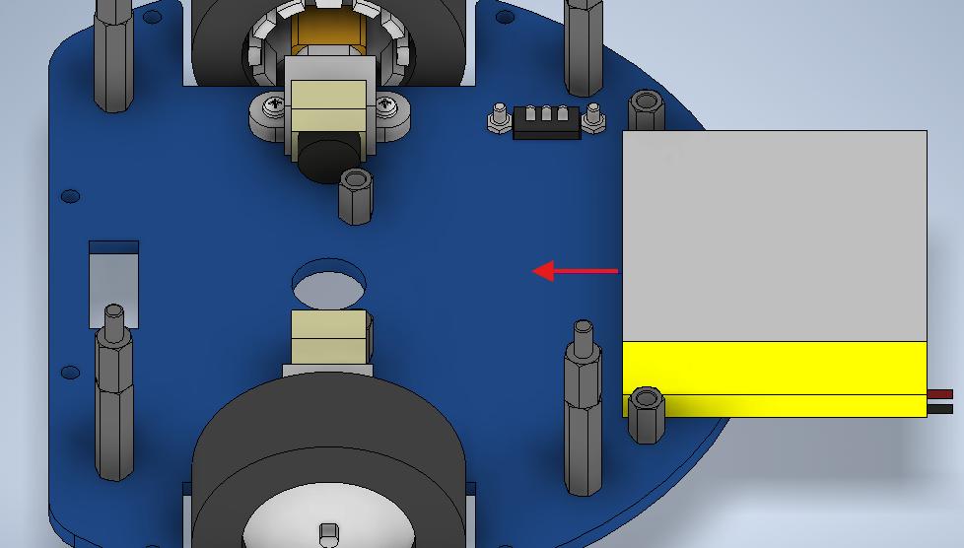
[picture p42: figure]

26

### 13. Conectar PowerBoost a base intermedia con tornillos M2 12 mm para

parte frontal de base y tornillos M2 8 mm para parte trasera. Ajustar primero los tornillos de parte trasera con tuercas M2 y nivele modulo con los tornillos frontales. Asegurarse que tornillos entren desde arriba y tuerca desde abajo. (Utilice Kit Precision).

Materiales:

- 2X Tornillos M2 12 mm
- 2X Tornillos M2 8 mm
- 8X Tuercas M2
- 1X Powerboost
- 1X Base intermedia

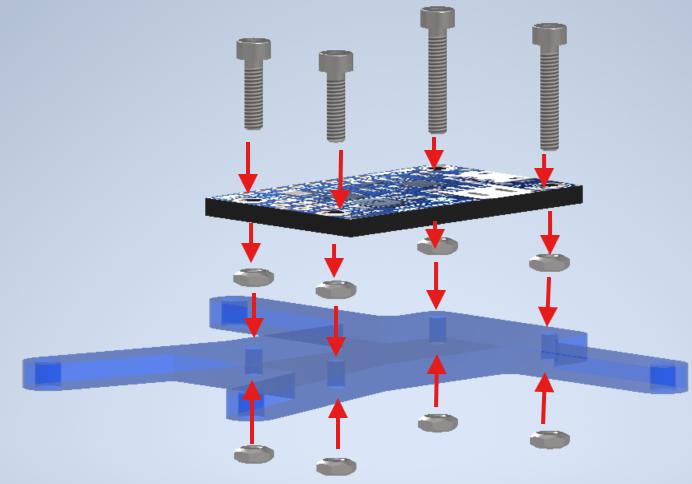
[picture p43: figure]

27

### 14. Conectar Base intermedia en espaciadores y encima de bateria de 3.7V con

tornillos M3 8 mm. (Utilice Kit Precision). Tomar cuidado de que ningún tornillo perfore la batería.

Materiales:

- 4X Tornillos M3 8 mm

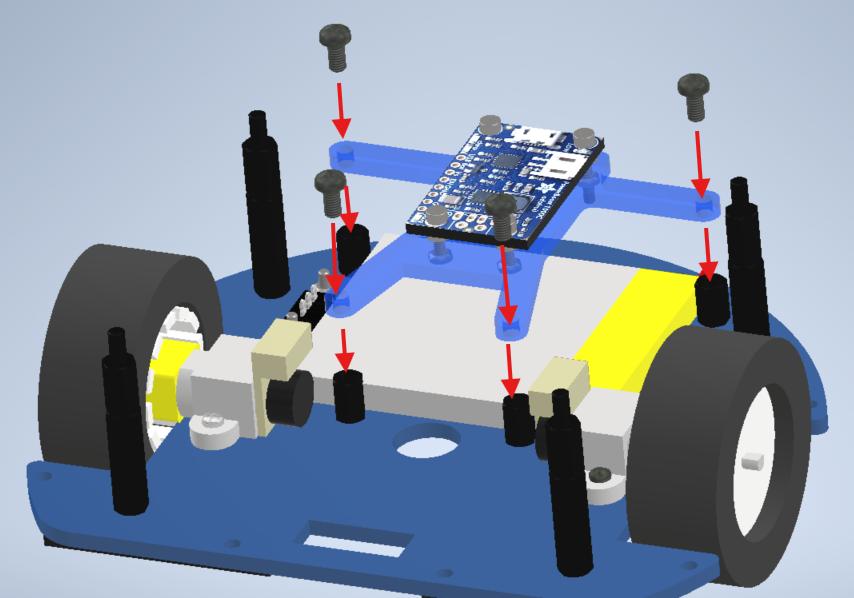
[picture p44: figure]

28

### 15. Conectar Switch a powerboost (pines 4 GND y 5 EN) y conectar Jumpers

Hembra-Hembra a powerboost (pines 1, 2 y 3 a 5V, GND y LB respectivamente). Conectar batería al powerboost.

Materiales:

- 3X Jumpers Hembra-Hembra

29

Resultado esperado al terminar la bolsa 2.

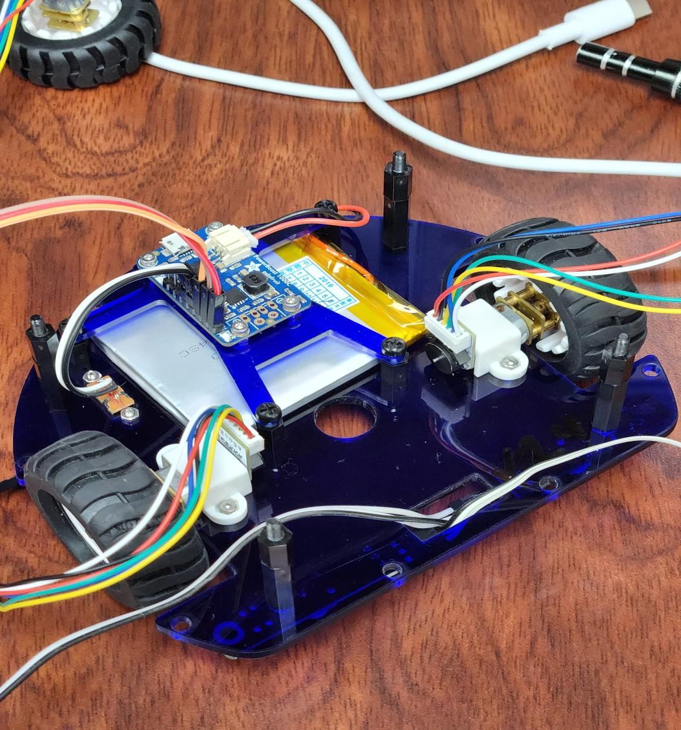
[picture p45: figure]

30

## Pasos de armado Bolsa 3

### 16. Conectar en base superior espaciadores M3 6+6 mm con tornillos M3 6

mm. Conectar espaciador con la tuerca por debajo de la base, y ajustar espaciador manualmente con la mano.

Materiales:

- 1X Base superior
- 4X Espaciador M3 6+6mm
- 4X Tuercas M3

31

32

### 17. Conectar espaciadores M3 6+6mm frontales con tornillos M3 6 mm

Materiales:

- 2X Espaciadores M3 6+6mm
- 2X Tornillos M3 6mm

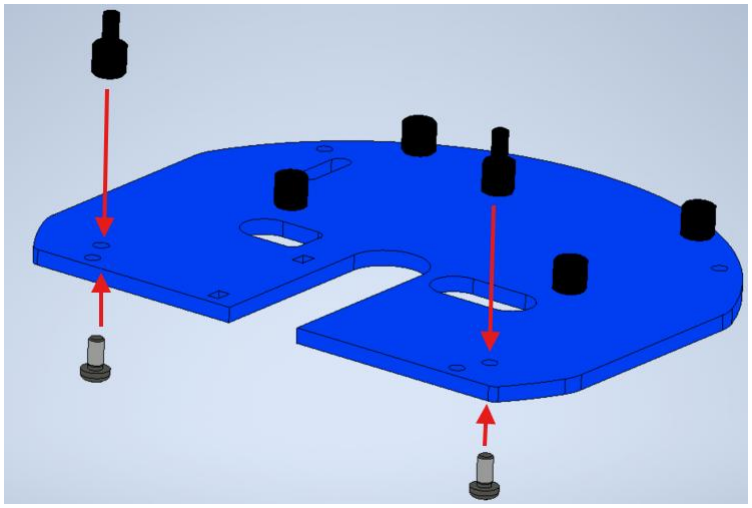
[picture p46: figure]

33

### 18. Ajustar base superior (parte trasera y parte delantera) con tuercas M3 en

espaciadores respectivos del robot. Recordar pasar jumpers en orificios designados para conexiones eléctricas seguidamente.

Materiales:

- 4X Tuercas M3

34

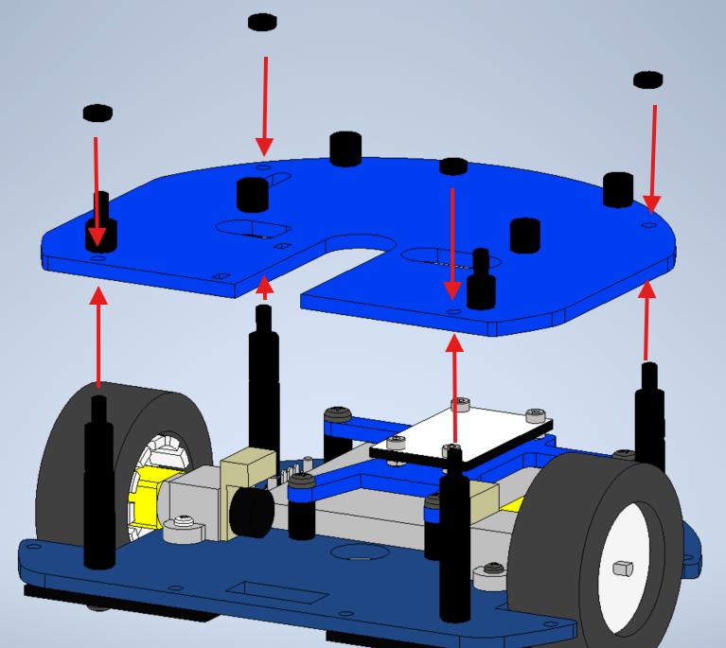
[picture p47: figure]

35

19. Conectar Ideaboard encima de los 4 espaciadores de la base superior. Ajustar componente con tornillos M3. (Utilice Kit Precision)

Materiales:

- 1X Ideaboard
- 4X Tornillos M3 6 mm

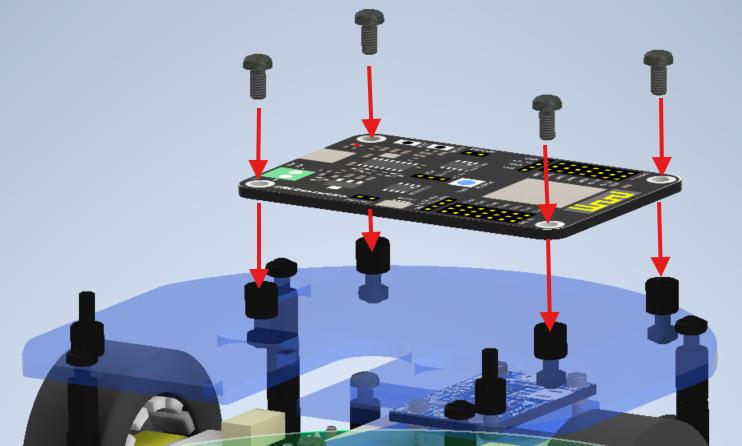
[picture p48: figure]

36

### 20. Conectar sensores infrarrojos delanteros en base superior. Montar sensor

encima de espaciador y ajustar con tuercas M3. (Utilice Kit Precision)

Materiales:

- 2X Sensores infrarrojos delanteros
- 2X Tuercas M3
- 6X Jumpers Hembra-Hembra

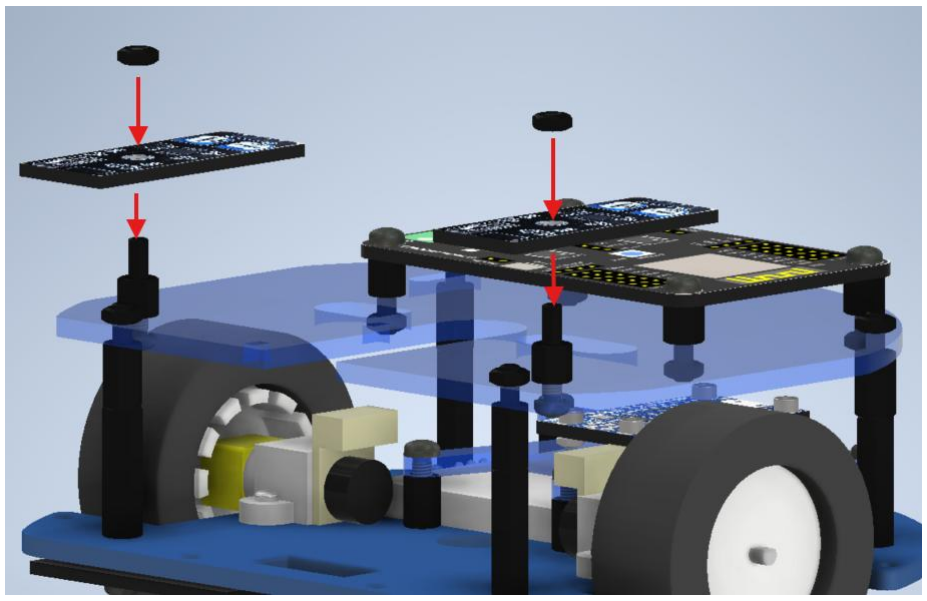
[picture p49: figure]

37

### 21. Tomar servomotor y ajustar soportes a este con tornillos M2 12 mm y

tuercas M2.

Materiales:

- 1X Servomotor
- 2X Tornillo M2 12 mm
- 2X Tuerca M2
- 2X Soporte Servomotor

38

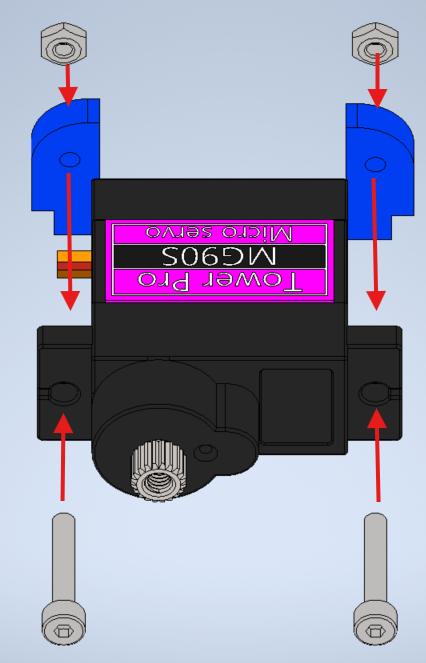
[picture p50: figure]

39

### 22. Tomar base de cremallera y ajustar la cremallera a esta con tornillos M3 8

mm y Tuercas M3. La cremallera debe ser capaz de deslizarse libremente. Asegurarse que los dientes de cremallera estén en dirección del centro de servomotor. (Utilice Kit Precision)

Materiales:

- 1X Base cremallera
- 1X Cremallera
- 2X Tornillos M3 8 mm
- 2X Tuercas M3

40

41

### 23. Ajustar base de cremallera en espacio designado de servomotor y ajustar

el engrane a la cremallera.

Materiales:

- 1X Engrane

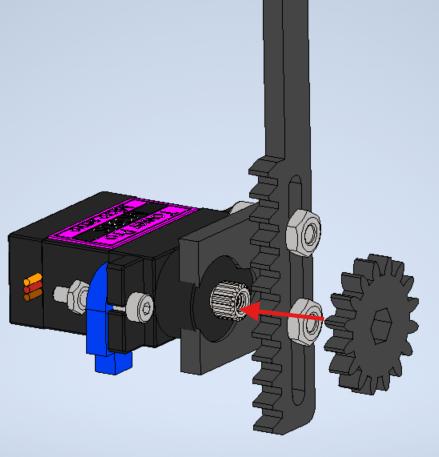
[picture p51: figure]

42

24. Ajustar prensa en la cremallera con tornillo M2 8 mm y una tuerca M2.

Materiales:

- 1X Prensa Pilot
- 1X Tornillo M2 8 mm
- 1X Tuerca M2

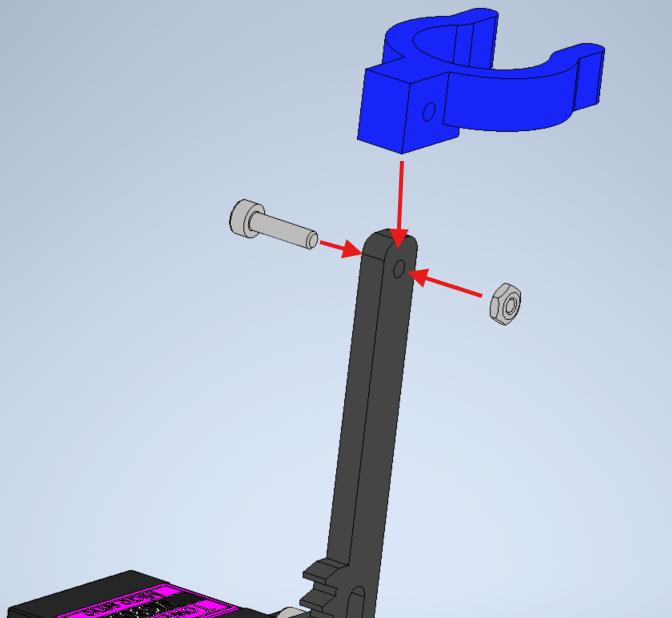
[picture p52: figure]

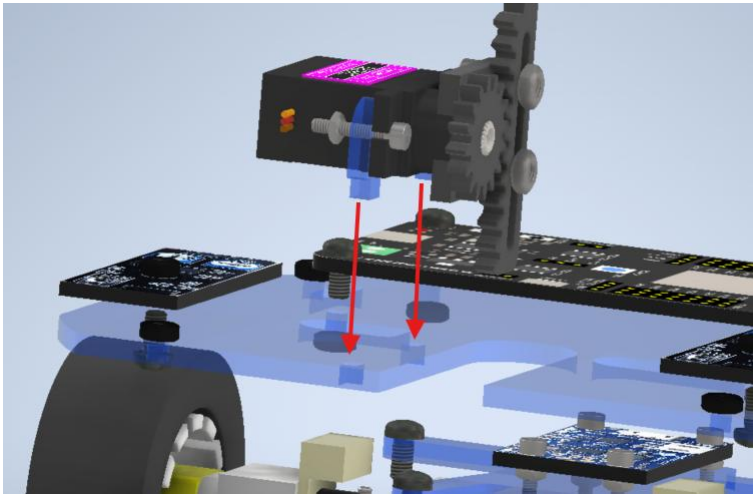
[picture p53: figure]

43

25. Montar servomotor en espacio designado de la base superior del robot.

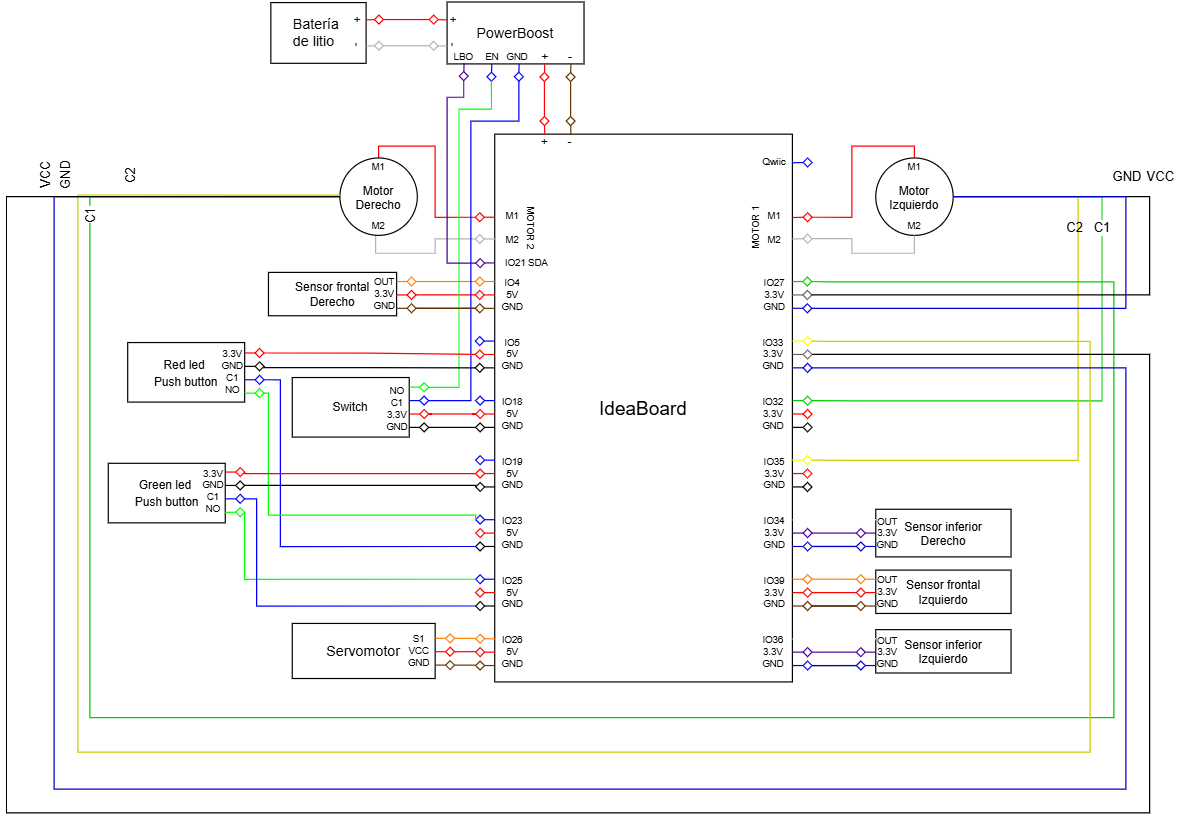
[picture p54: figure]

44

26. Realizar las conexiones eléctricas del microcontrolador según el diagrama.

45

### 27. Montar carcasa de robot en base y ajustar con tornillos M3 10 mm

Materiales:

- 1X Carcasa Robot
- 4X Tornillos M3 10 mm

46

Resultado esperado al terminar la bolsa 3.

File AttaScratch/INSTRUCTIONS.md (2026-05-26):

# Develop your own Scratch extension

- **Create your account**
  - [Create an account on GitHub](#create-an-account-on-github)
- **Setup your development environment**
  - [Create your Scratch repository](#create-your-scratch-development-repository)
  - [Go into Codespaces](#launch-codespaces)
  - [Set up repository](#set-up-your-repository)
- **Create your extension**
  - [Create a block using live data from an online API](#create-a-block-using-live-data)
  - [Create a block using a JavaScript module from npm](#create-a-block-using-a-javascript-module)
  - [Customize the Extension Menu](#customize-the-extensions-menu)
- **Publish your extension**
  - [Publish your Scratch extension](#publish-your-finished-extension)
  - [Stop your codespace](#stop-your-codespace)

---

## Create an account on GitHub

_**If you already have a GitHub account, you can [skip to the next step](#create-your-scratch-development-repository).**_

Go to https://github.com

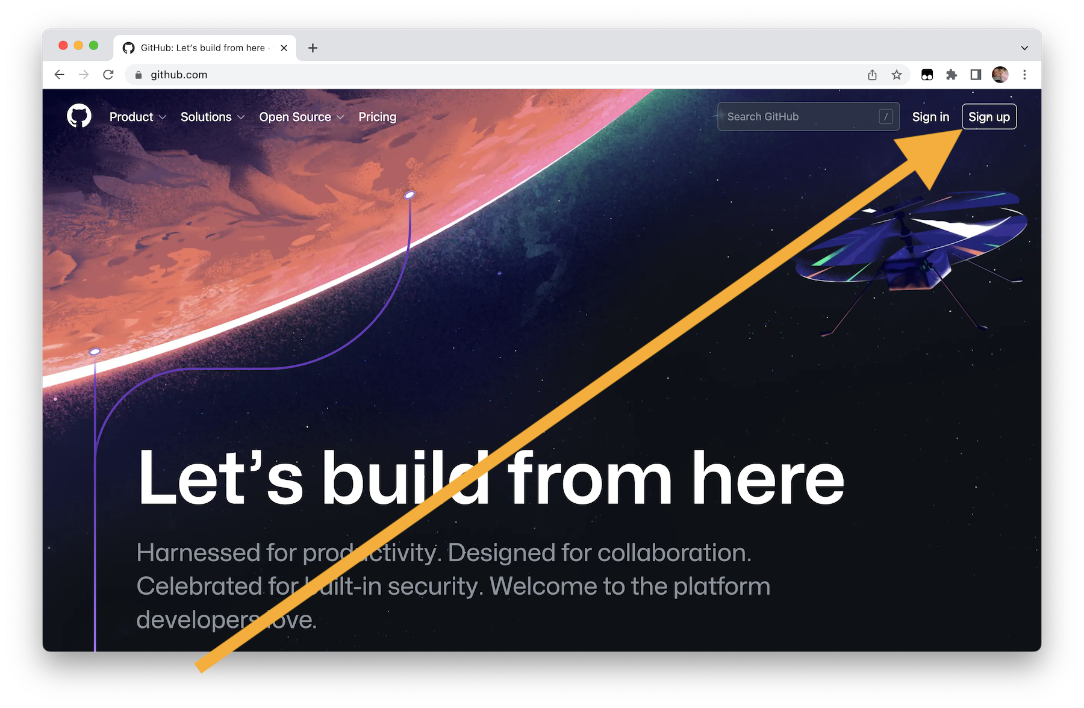
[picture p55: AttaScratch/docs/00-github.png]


Click on **Sign up**

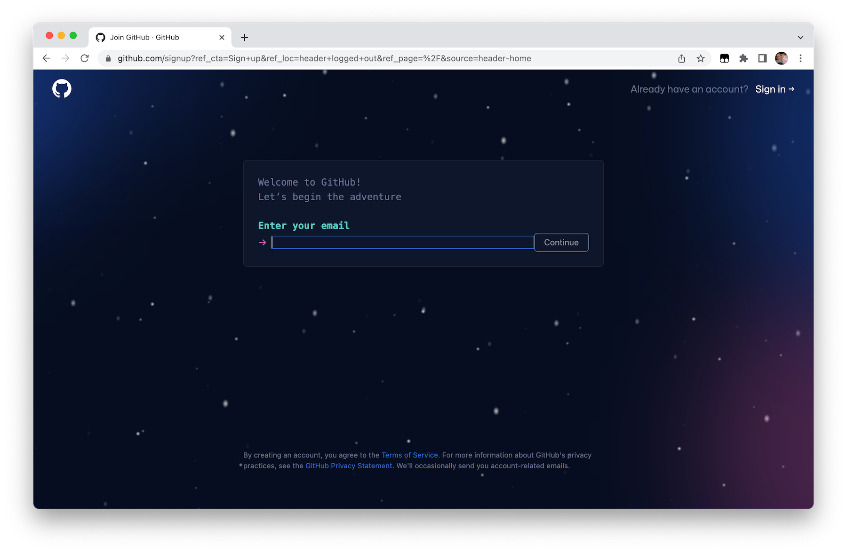
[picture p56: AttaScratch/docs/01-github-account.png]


Create your account

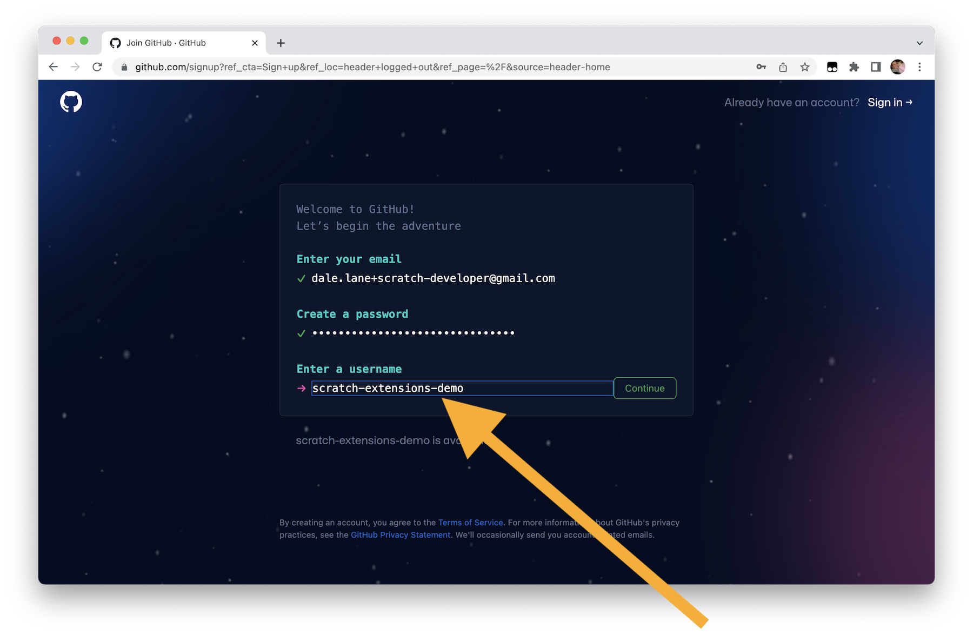
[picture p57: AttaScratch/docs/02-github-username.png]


Note that your GitHub **username** will be part of the web address for your modified Scratch fork, so you may want to keep that in mind when you choose your username.

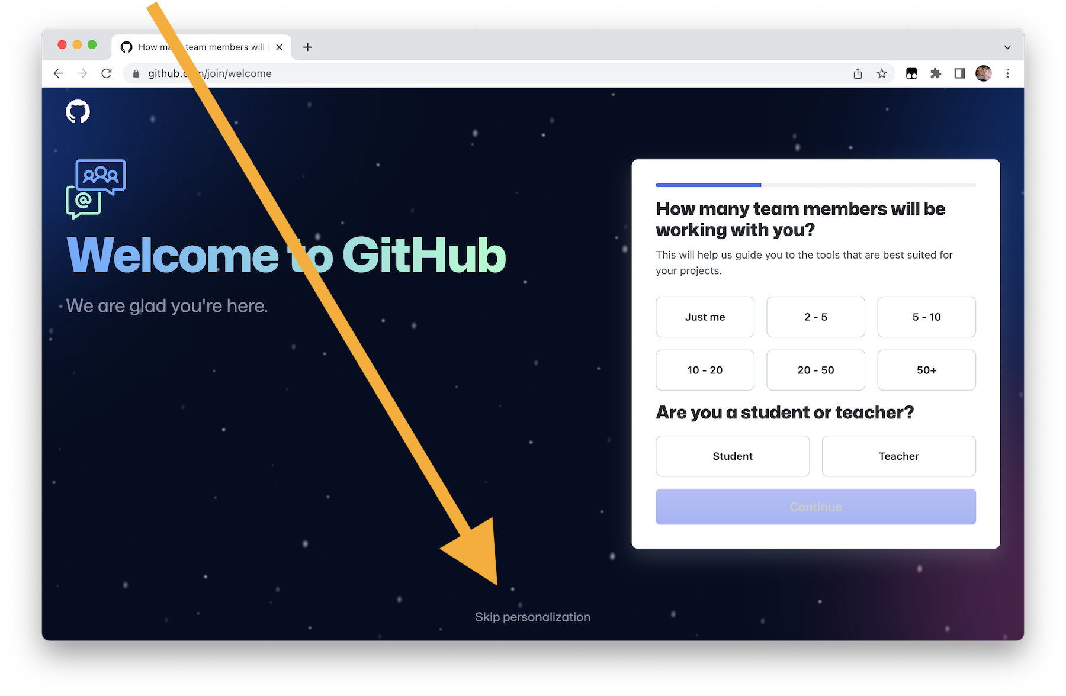
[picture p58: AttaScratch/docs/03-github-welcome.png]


When you get to the **Welcome** screen, you can fill in the personalization survey if you wish, but it is okay to click on the **Skip personalization** link at the bottom of the screen if you prefer.

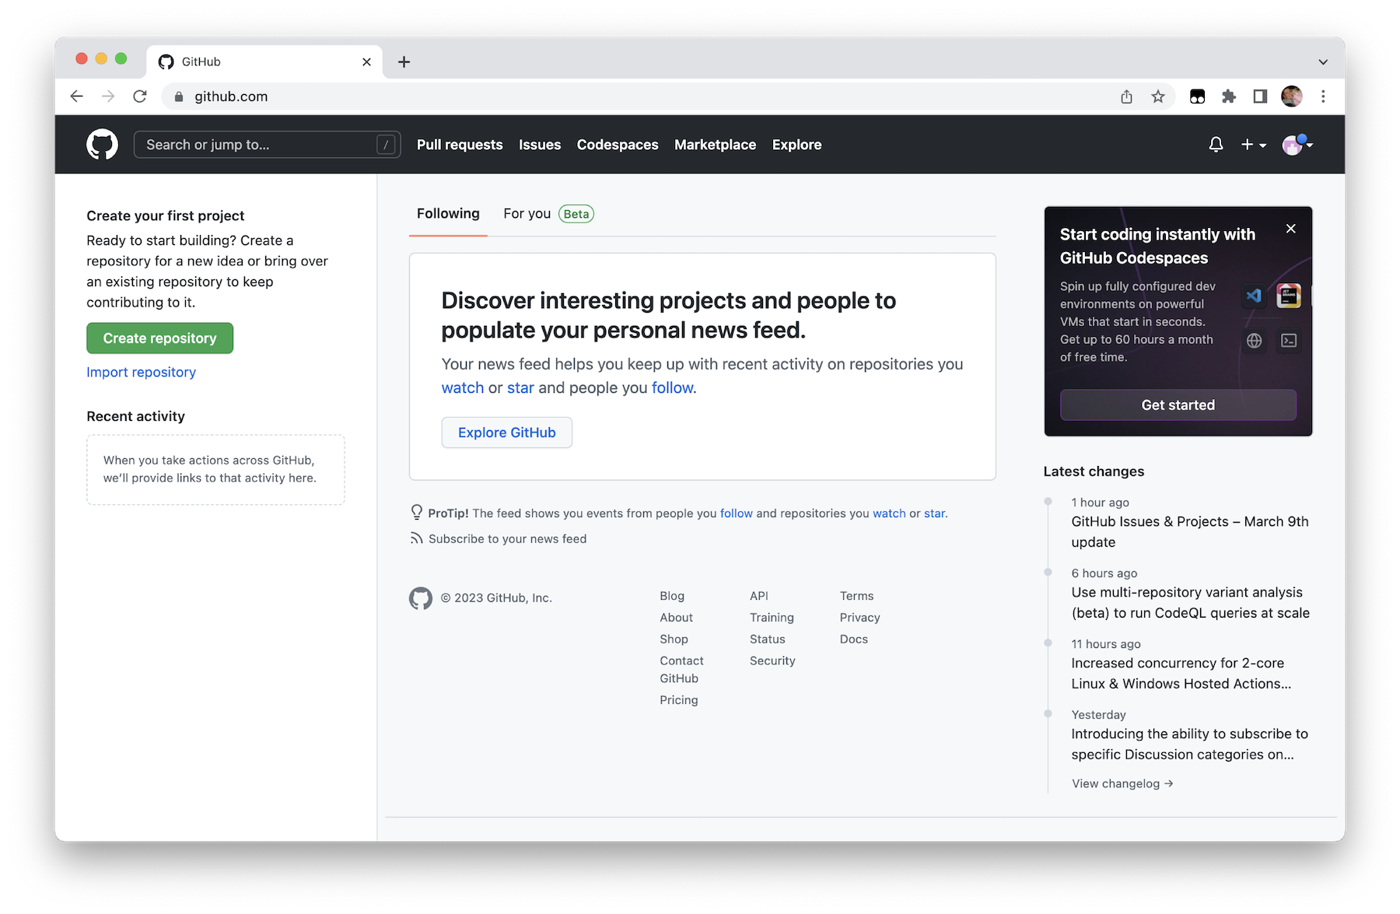
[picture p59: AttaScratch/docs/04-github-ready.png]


You should now have a GitHub account, ready to create your Scratch repository.

---

## Create your Scratch development repository

Go to https://github.com/dalelane/scratch-extension-development

_If you aren't already logged into GitHub, you should log in now._

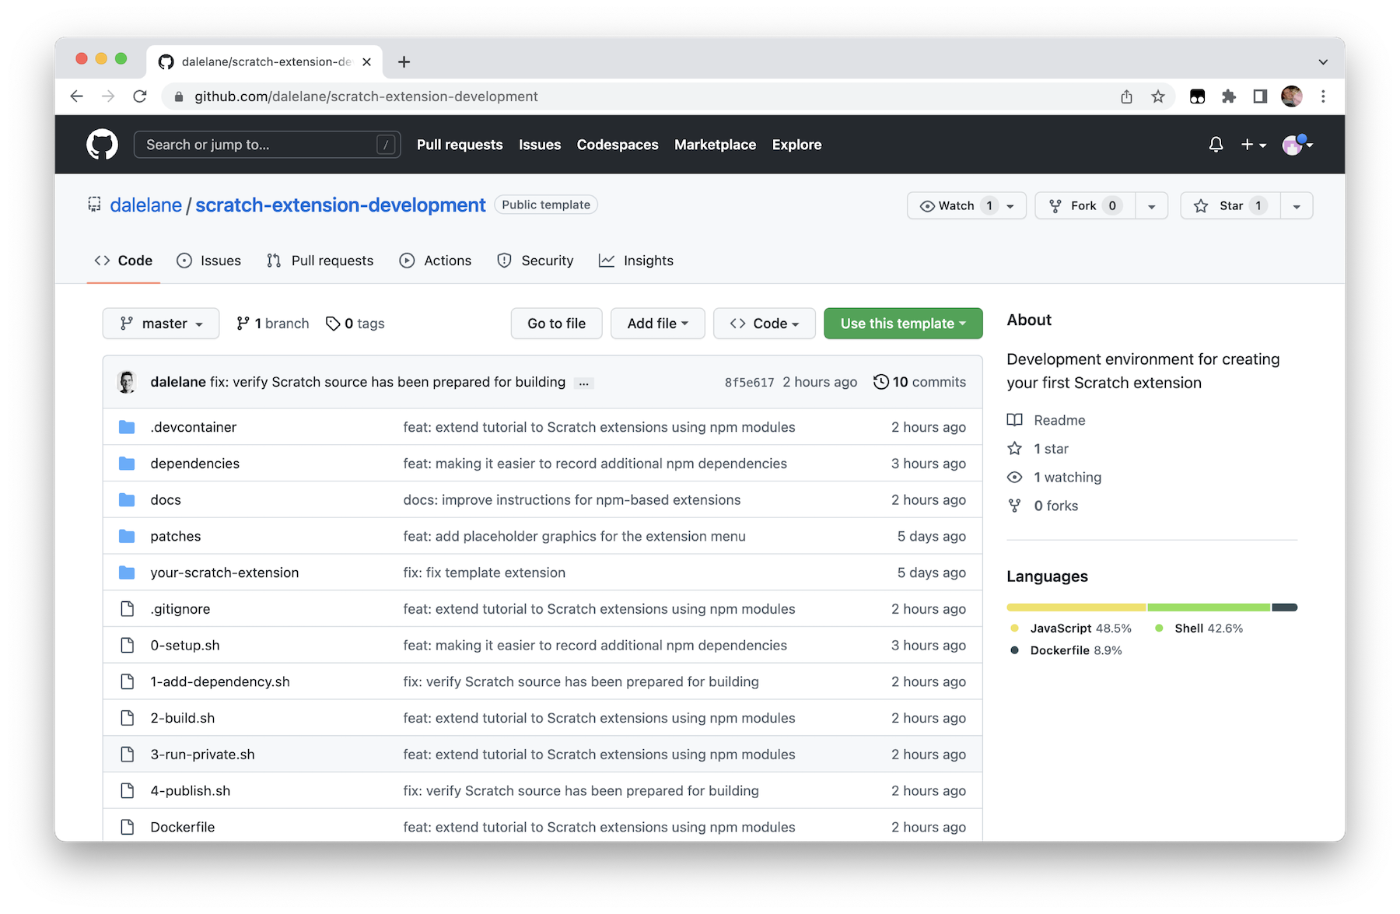
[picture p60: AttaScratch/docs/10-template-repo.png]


Click on **Use this template** and then choose **Create a new repository**

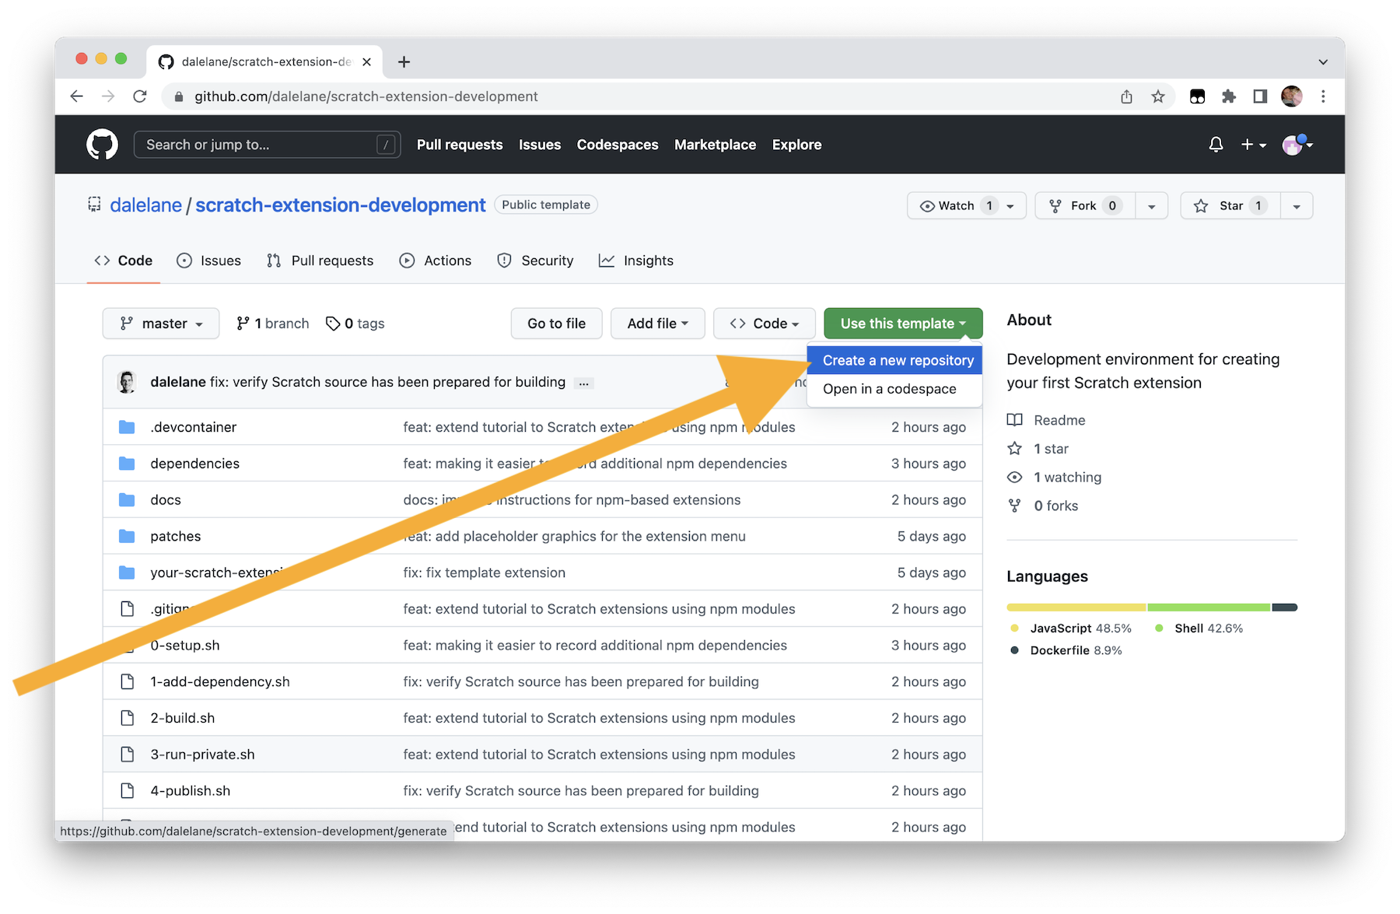
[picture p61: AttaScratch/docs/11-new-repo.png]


Give your new repository a name.

Note that the repository name will be part of the web address for your modified Scratch fork, so you may want to keep that in mind when you choose a name.

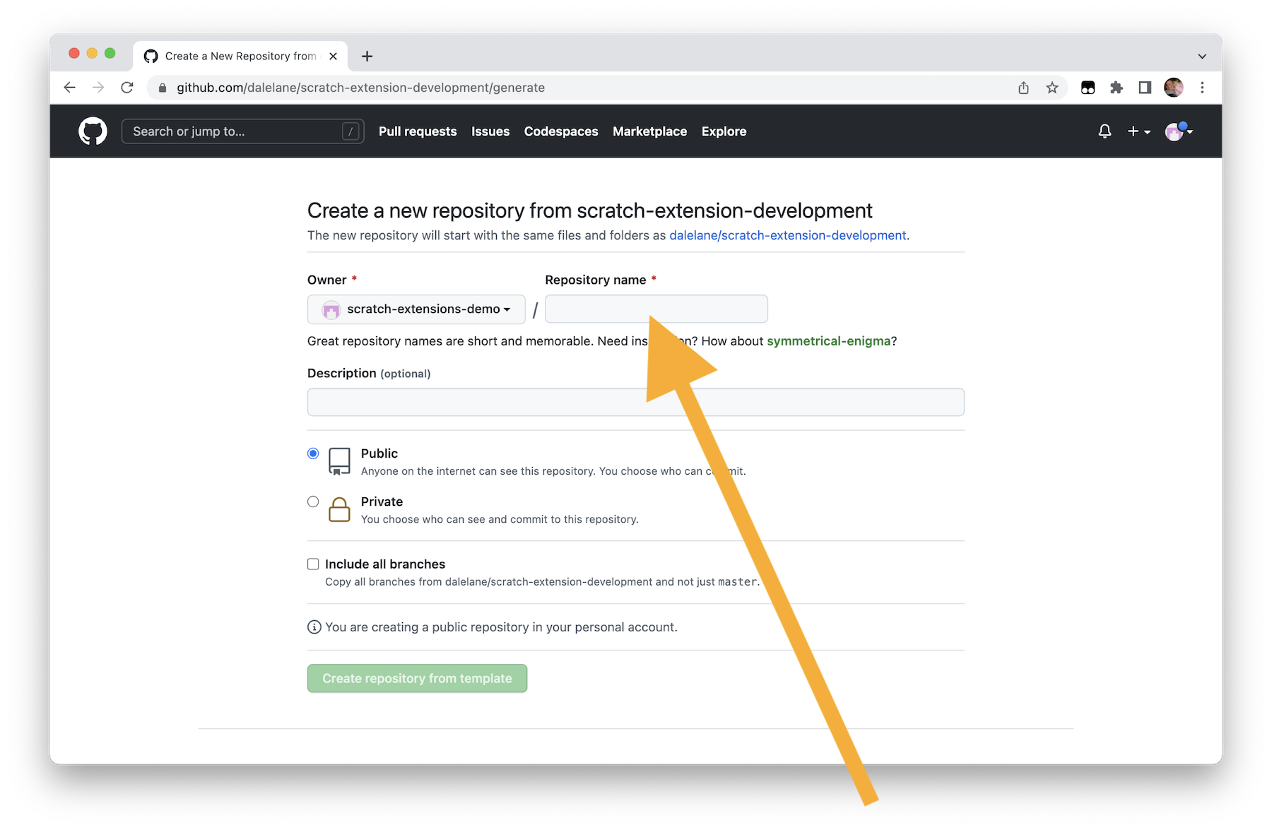
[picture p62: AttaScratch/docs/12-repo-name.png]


Your repository is ready for use.

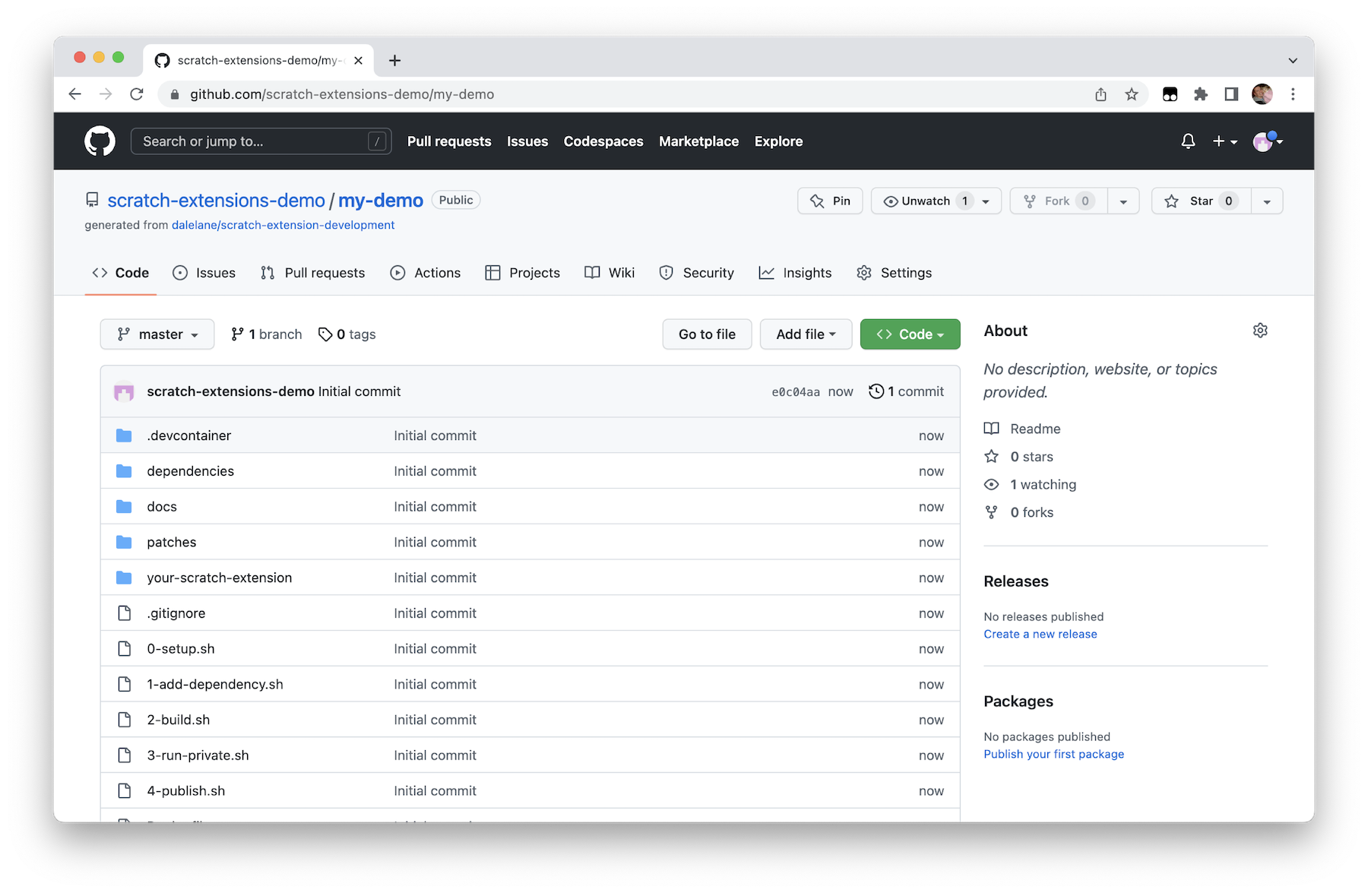
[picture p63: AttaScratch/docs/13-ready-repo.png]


---

## Launch codespaces

Click on **Code** -> **Codespaces** -> **Create codespace**

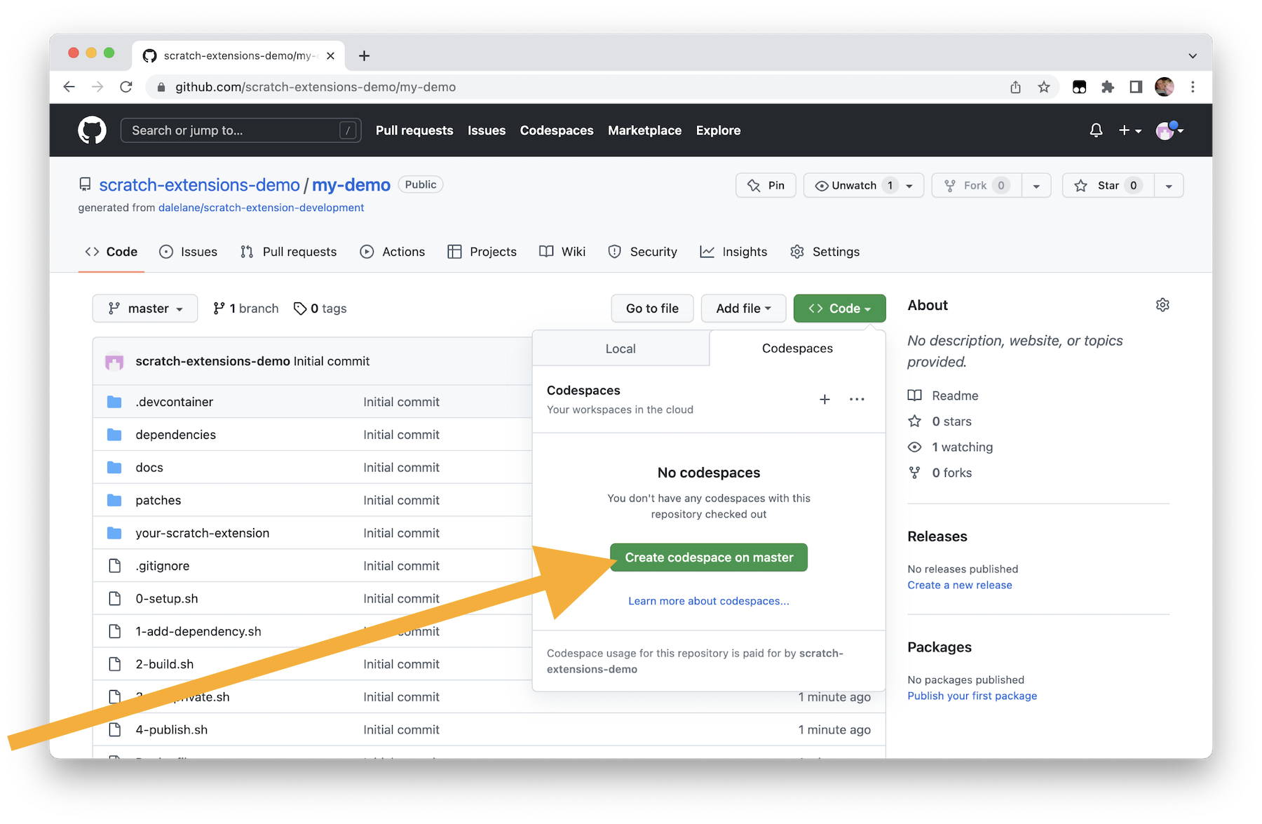
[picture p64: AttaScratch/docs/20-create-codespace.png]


It can take a minute or two to set up your codespace.

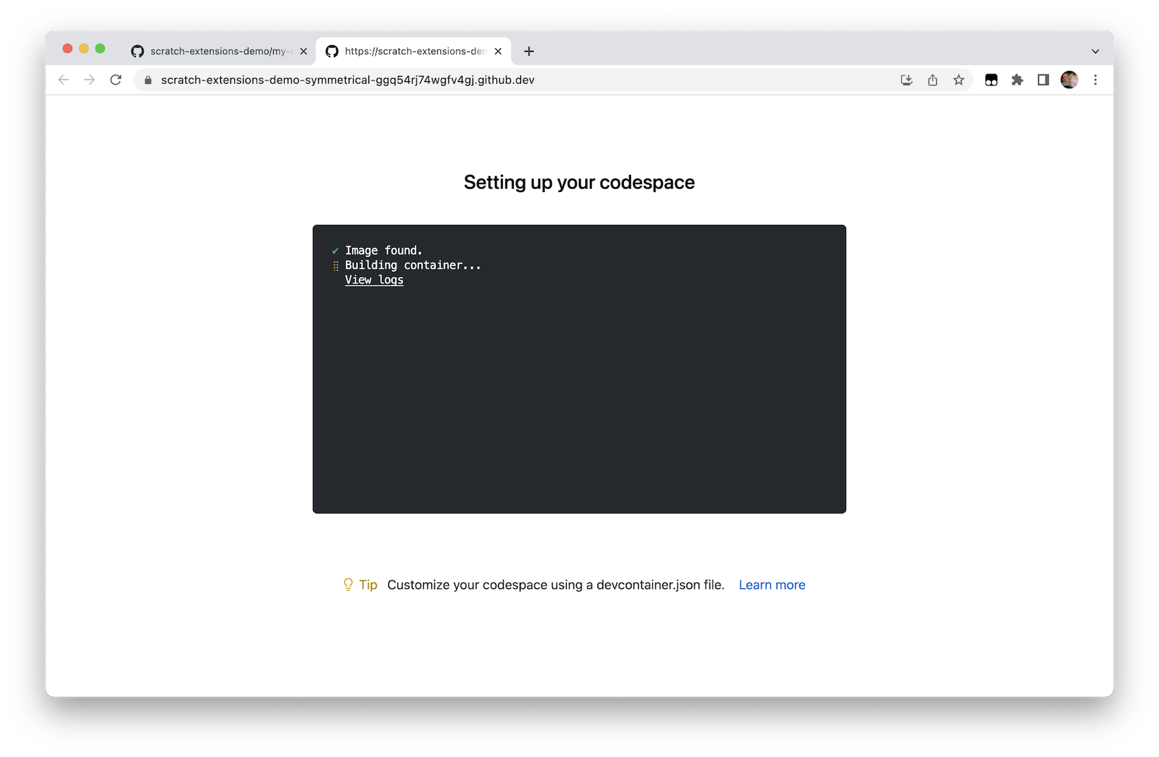
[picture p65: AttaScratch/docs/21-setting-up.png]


Your codespace is ready for use.

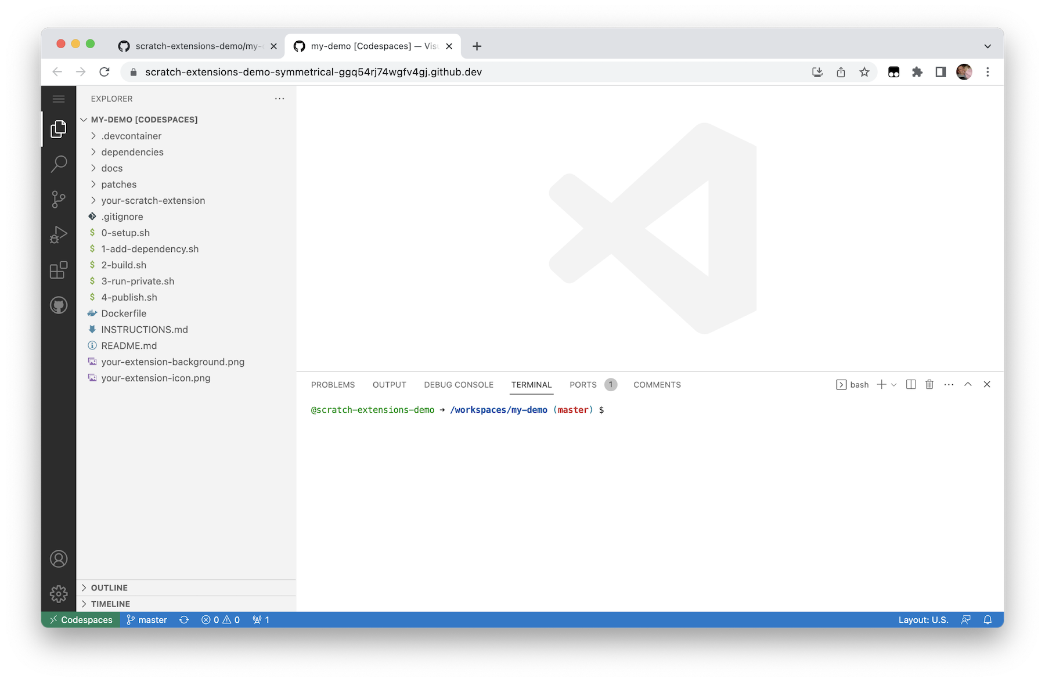
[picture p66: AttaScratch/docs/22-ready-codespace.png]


---

## Set up your repository

In the terminal at the bottom of the window, run:
```sh
./0-setup.sh
```

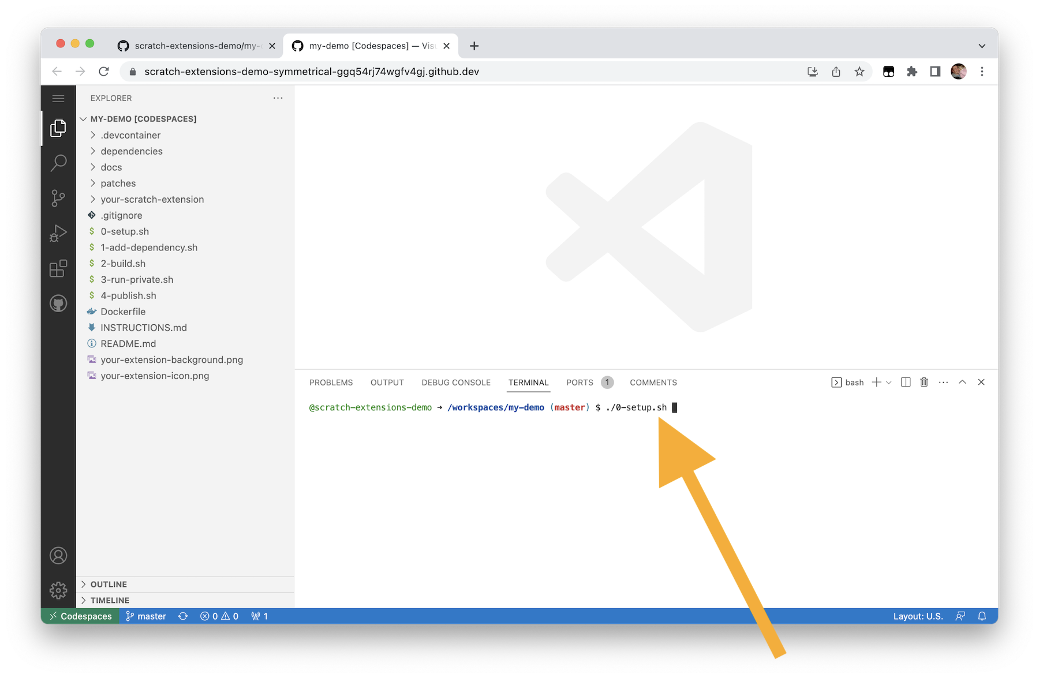
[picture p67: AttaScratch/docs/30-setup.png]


This should be very quick.

You only need to do this once (but it is safe if you run it again).

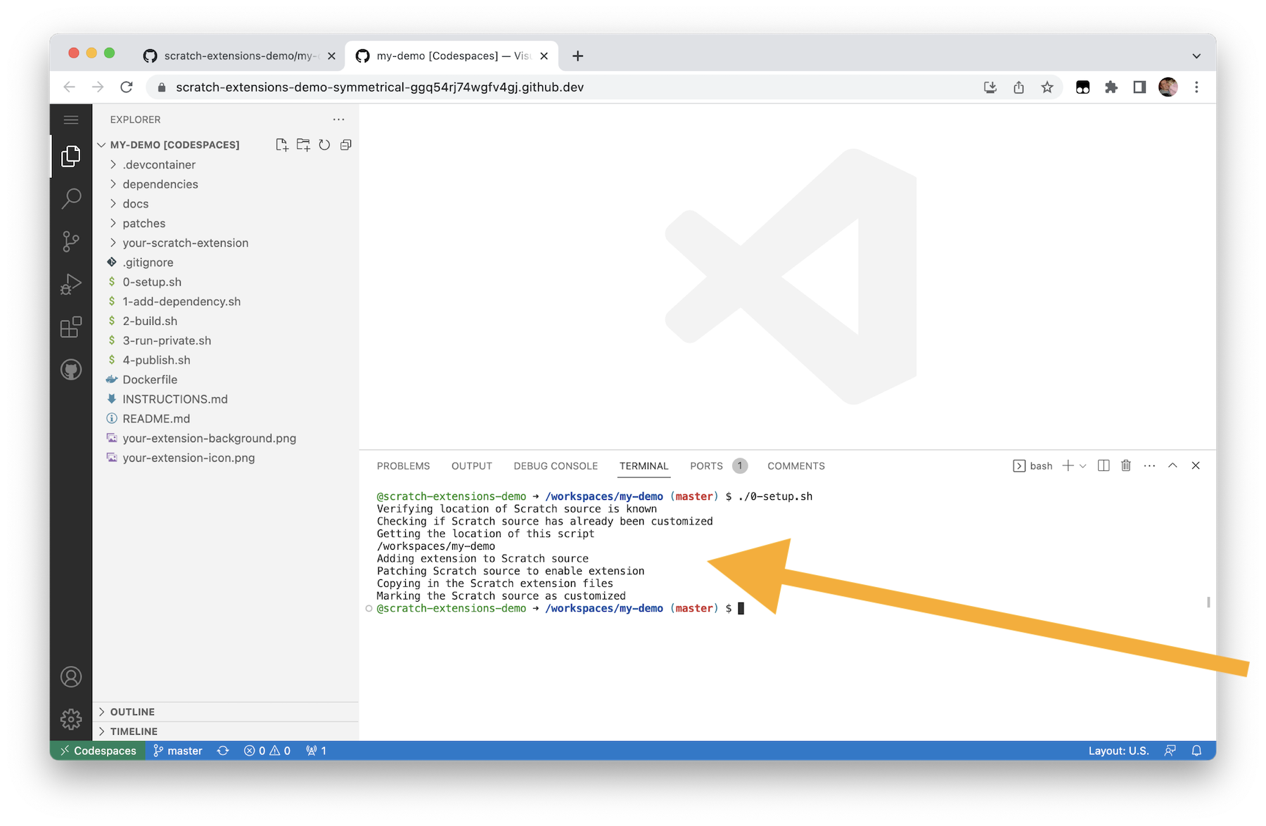
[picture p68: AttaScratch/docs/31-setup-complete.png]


---

## Create a block using live data

**The instructions here will show you how to write an extension that can lookup the title of a book from the ISBN number, using an online API.**

The instructions will go through the template JavaScript one section at a time.

Open the `your-scratch-extension/index.js` file.

Review the sample extension to see the sort of options that are available to you.

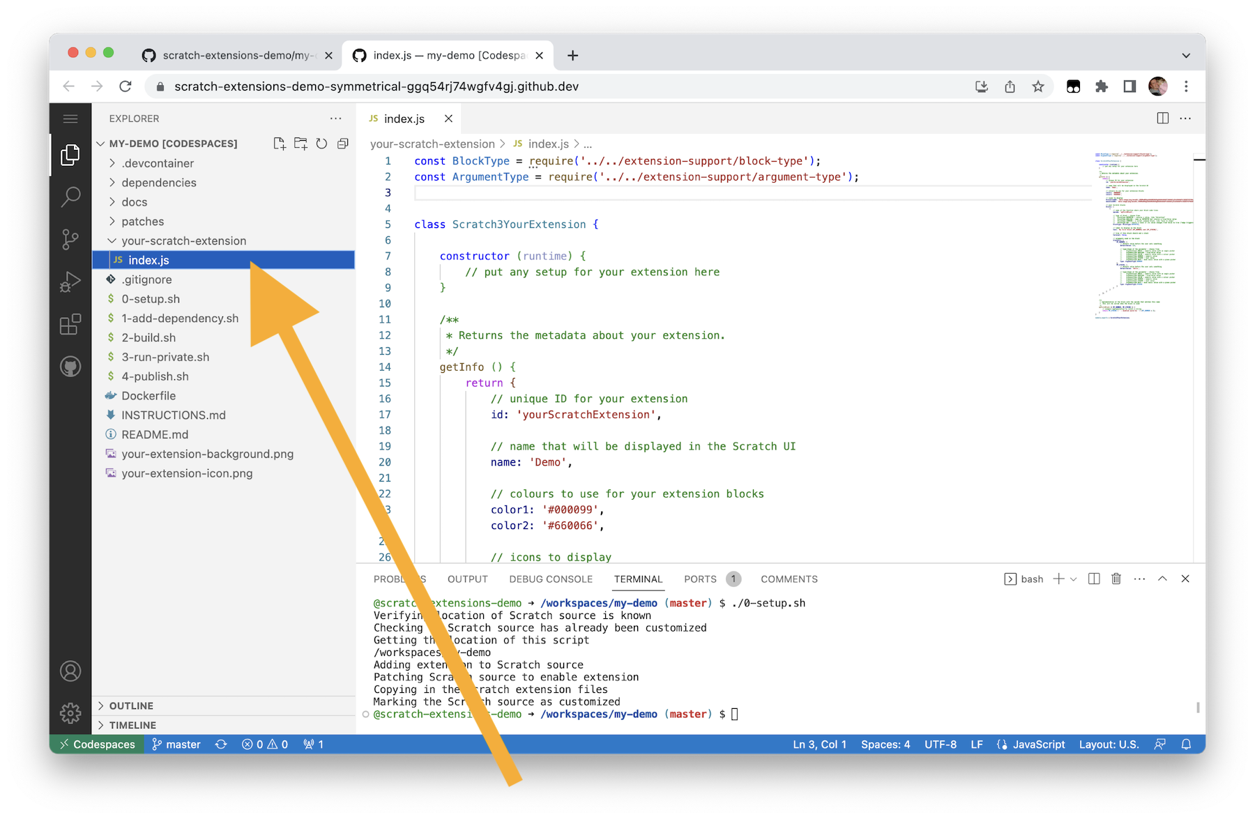
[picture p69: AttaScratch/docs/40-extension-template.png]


Edit the `getInfo()` function to provide a description of your first block.

```js
getInfo () {
  return {
    // unique ID for your extension
    id: 'yourScratchExtension',

    // name displayed in the Scratch UI
    name: 'Demo',

    // colours to use for your extension blocks
    color1: '#000099',
    color2: '#660066',
    color3: '#000000',

    // your Scratch blocks
    blocks: [
      {
        // function where your code logic lives
        opcode: 'myFirstBlock',

        // type of block
        blockType: BlockType.REPORTER,

        // label to display on the block
        text: 'Title for ISBN book [BOOK_NUMBER]',

        // arguments used in the block
        arguments: {
          BOOK_NUMBER: {
            defaultValue: 1718500564,

            // type/shape of the parameter
            type: ArgumentType.NUMBER
          }
        }
      }
    ]
  };
}
```

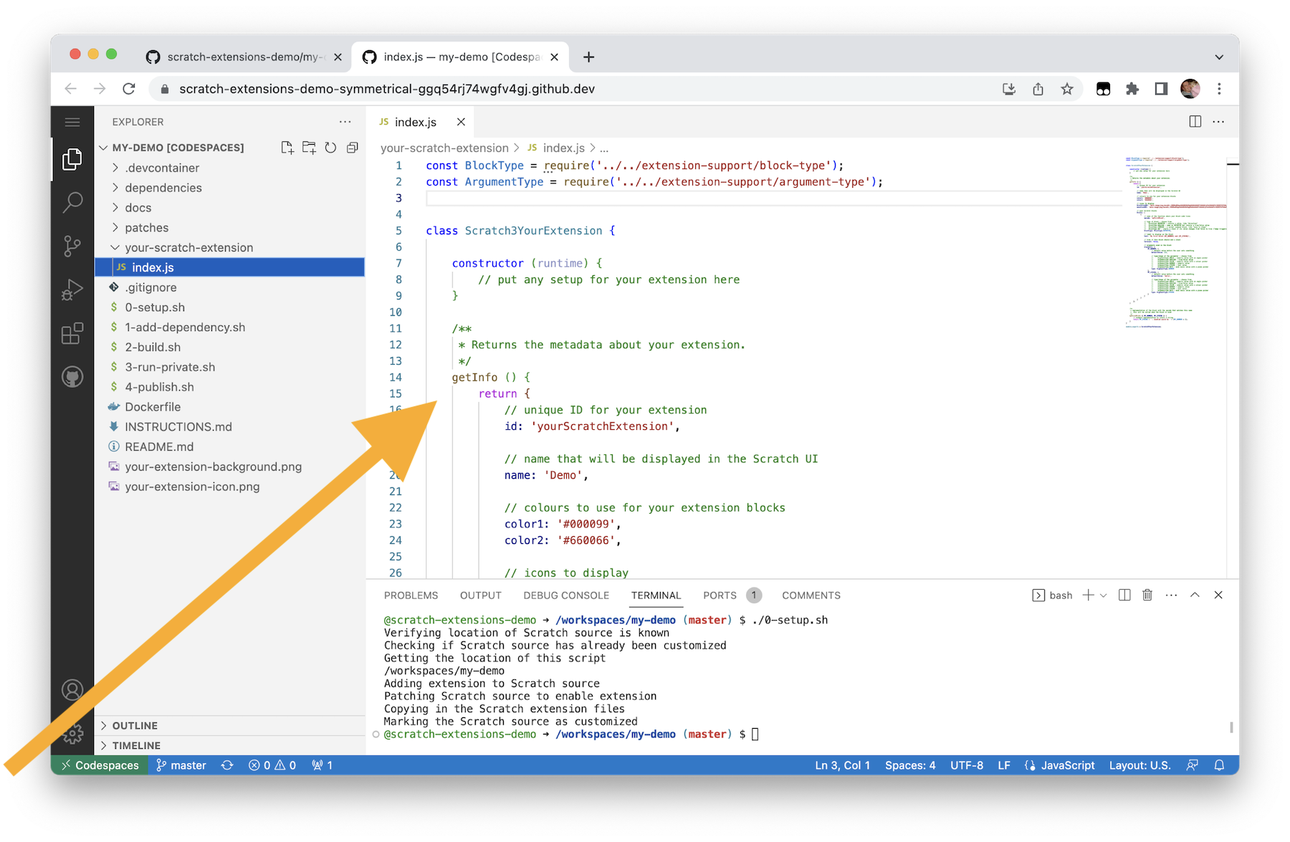
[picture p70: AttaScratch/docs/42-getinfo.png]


Edit the `myFirstBlock` function implementation to look up book info using the [OpenLibrary API](https://openlibrary.org/dev/docs/api/books).

```js
myFirstBlock ({ BOOK_NUMBER }) {
  return fetch('https://openlibrary.org/isbn/' + BOOK_NUMBER + '.json')
    .then((response) => {
      if (response.ok) {
        return response.json();
      }
      else {
        return { title: 'Unknown' };
      }
    })
    .then((bookinfo) => {
      return bookinfo.title;
    });
}
```



Your code is now ready to test.

---

## Launch a private test of your Scratch extension

In the terminal at the bottom of the window, run:
```sh
./2-build.sh
```



This can take a minute to run. Wait for this to complete.

In the terminal at the bottom of the window, run:
```sh
./3-run-private.sh
```



A pop-up should appear in the bottom-right with a button to open a private window with your modified version of Scratch.



If it doesn't appear, or you accidentally dismiss it, you can get the link from the **Open in browser** button on the **Ports** tab.



Either way, click on **Open in browser**.



This is a private copy of Scratch that only you can access. You can use this to test your new extension.

Click on the **Extensions** button.



You should see your extension added to the menu. Click on it.



Make a simple Scratch project using your extension.



If you need to make a change, stop your Scratch test by pressing **Control-C** in the terminal.

Make your code changes.

Then re-build and test again by typing:
```sh
./2-build.sh
./3-run-private.sh
```

Once you have finished, stop your Scratch test by pressing **Control-C** in the terminal.



---

## Create a block using a JavaScript module

**The instructions here will show you how to write an extension that can estimate the number of syllables in some English text, using a JavaScript module.**

The instructions will go through the template JavaScript one section at a time.

Select a module from https://www.npmjs.com - for this example, I'm using `syllable`.



Run `./1-add-dependency.sh` with the name of the module you've selected.
```sh
./1-add-dependency.sh syllable
```



As long as you have spelled it exactly correctly, it will update the dependencies for your private Scratch build to include the new module.

_If you want to add multiple dependencies, you can run this script multiple times. Running the script with the name of a dependency you have already added is safe, but not necessary._



Open the `your-scratch-extension/index.js` file again.

Edit the `constructor` function to load the module.
```js
constructor (runtime) {
  import('syllable')
    .then((syllableModule) => {
      this.syllable = syllableModule.syllable;
    });
}
```



Edit the `getInfo()` function to add a second block, after the block we defined before.

The complete `getInfo()` function will now contain:

```js
getInfo () {
  return {
    // unique ID for your extension
    id: 'yourScratchExtension',

    // name displayed in the Scratch UI
    name: 'Demo',

    // colours to use for your extension blocks
    color1: '#000099',
    color2: '#660066',
    color3: '#000000',

    // your Scratch blocks
    blocks: [
      {
        // function where your code logic lives
        opcode: 'myFirstBlock',

        // type of block
        blockType: BlockType.REPORTER,

        // label to display on the block
        text: 'Title for ISBN book [BOOK_NUMBER]',

        // arguments used in the block
        arguments: {
          BOOK_NUMBER: {
            defaultValue: 1718500564,

            // type/shape of the parameter
            type: ArgumentType.NUMBER
          }
        }
      },
      {
        // function where your code logic lives
        opcode: 'mySecondBlock',

        // type of block
        blockType: BlockType.REPORTER,

        // label to display on the block
        text: 'Syllables in [MY_TEXT]',

        // arguments used in the block
        arguments: {
          MY_TEXT: {
            defaultValue: 'Hello World',

            // type/shape of the parameter
            type: ArgumentType.STRING
          }
        }
      }
    ]
  };
}
```



Add a `mySecondBlock` function implementation to return a count of syllables using the loaded npm module.

```js
mySecondBlock ({ MY_TEXT }) {
  return this.syllable(MY_TEXT);
}
```



Your code is now ready to test.

As before, build your code:

```sh
./2-build.sh
```



Then run a private instance of Scratch to test it.

```sh
./3-run-private.sh
```



When prompted, click on the **Open in browser** button to open your private Scratch instance.



You can make a simple Scratch script to verify that your new block is working.



When you've finished your test, close the Scratch window, and then stop the test instance by pressing **Control-C** in the Terminal.



---

## Customize the Extensions menu

The extensions menu includes images to represent each extension. Each extension has a large background image, and a small inset icon.

Placeholder images are provided for your extension.



If you're happy with these, you can [skip to the next step](#publish-your-finished-extension).

If you want to customize these, you can edit the image files `your-extension-background.png` and `your-extension-icon.png` to better represent your Scratch extension.



I recommend keeping the dimensions of the images the same as they currently are to best fit in the menu.

Note that you will need to rebuild your extension after making changes to these files.

```sh
./2-build.sh
```

And to see the new menu in action you will want to start your private test instance again.

```sh
./3-run-private.sh
```

Before proceeding to the next step, make sure you have stopped your private test instance of Scratch by pressing **Control-C** in the terminal.



---

## Publish your finished extension

In the terminal at the bottom of the window, run:
```sh
./4-publish.sh
```



This can take a minute to run.



Your Scratch fork will be live and publicly accessible at:

```
https://<YOUR-GITHUB-USERNAME>.github.io/<YOUR-REPOSITORY-NAME>/scratch
```

For example, in my screenshots I created a GitHub account with the username `scratch-extensions-demo` and when I forked the repository, I named it `my-demo`.



_Note that this can sometimes take a minute to go live, so if the link doesn't work, it's worth waiting a minute and trying again. (But if it still doesn't work, check you have got the URL correct!)_



You can give this URL to your students.



---

## Stop your codespace

You only need your codespace running while you are developing your extension. Once it's published, you must stop your codespace.

On your repository page, click on **Code** -> **Codespaces** -> **Stop codespace**.



Your published Scratch instance, with your extensions, will still be accessible after you do this.



---

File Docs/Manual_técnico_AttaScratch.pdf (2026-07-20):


# Guía de usuario: Proyecto AttaScratch

## Version 1.0

## José Carlos Gutiérrez Zúñiga

12 de junio de 2026

## Índice

1. Introducción | 2
2. Requerimientos | 2
3. Instalación y configuración | 3
4. Interfaz de usuario | 4
5. Operaciones básicas de AttaScratch | 5
6. Funcionalidades avanzadas | 7
7. Problemas comunes | 9
8. Soporte y recursos | 10

1

## 1. Introducción

### 1.1. Propósito del software:

AttaScratch es un ambiente de programación para controlar y simular secuencias de AttaBot-STEM desarrollado por el laboratorio GIRoM del Instituto Tecnológico de Costa Rica.

El proyecto de AttaScratch cuenta con dos partes principales. La primera es el ambiente de desarrollo de extensiones no oficiales de Scratch¹ (https://github.com/scratch-extension/scratchextension) del cual se basa el repositorio de AttaScratch² (https://github.com/Jocaguz/AttaScratch) para editar, construir y publicar la aplicación de AttaScratch.

La segunda es la aplicación resultante AttaScratch³ (https://jocaguz.github.io/AttaScratch/scratch/)
la cual es el software
que los usuarios del AttaBot-STEM interactúan.

### 1.2. Público objetivo

Este manual esta dirigido a los integrantes del laboratorio GIRoM para que realicen el desarrollo, mantenimiento y uso del proyecto AttaScratch.

## 2. Requerimientos

Se aclara que estos requerimientos son para utilizar todas las funcionalidades de AttaScratch, específicamente el control del AttaBot-STEM. Para programar en el ambiente de desarrollo o utilizar AttaScractch solo se requiere cualquier navegador web moderno.

### 2.1. Hardware

Dispositivo con tarjeta de Bluetooth con soporte del estándar 4.0 o superior para uso del Bluetooth Low Energy

### 2.2. Software

Navegador Web con soporte del paquete de Web Bluetooth

1https://github.com/scratch-extension/scratchextension2https://github.com/Jocaguz/AttaScratch3https://jocaguz.github.io/AttaScratch/scratch/

2

- Para Windows, McOS y Linux se recomienda ungloogled Chromiun⁴ (https://ungoogled-software.github.io/ungoogled-chromium-binaries/)
, Chrome o Edge.
- Para Android se recomienda ungloogled Chromiun⁵ (https://github.com/ungoogled-software/ungoogled-chromium-android) o Chrome.
- Para iOS (iPhones y iPads) se recomienda Bluefy - Web BLE Browser⁶ (https://apps.apple.com/us/app/bluefy-web-ble-browser/id1492822055)

## 3. Instalación y configuración

AttaScratch⁷ (https://jocaguz.github.io/AttaScratch/scratch/) es una aplicación Web y el ambiente de desarrollo genera el hosting automáticamente al utilizar ./4-publish.sh. Por lo que se puede utilizar con sencillamente ingresar a su dirección web.

### 3.1. Pasos de instalación local

Para utilizar AttaScratch de manera local se tienen se tienen dos opciones:

1. Paquete de ralease⁸ (https://github.com/Jocaguz/AttaScratch/releases)
: En el repositorio de Github se encuentra un .zip con todos los archivos necesarios para su uso offline
2. Repositorio de Github pages⁹ (https://github.com/Jocaguz/AttaScratch/tree/gh-pages)
: desde el branch para el hosting se puede descargar el repositorio completo con la versión más reciente del build de AttaScratch. La aplicación es la carpeta scratch

La primera opción es la más conveniente y útil para la mayoría de usuarios. La opción dos es para quien realiza actualizaciones en AttaScratch y actualice el build localizado en raleases.

En ambos casos para ejecutar AttaScratch se le da doble click al index.html

4https://ungoogled-software.github.io/ungoogled-chromium-binaries/5https://github.com/ungoogled-software/ungoogled-chromium-android6https://apps.apple.com/us/app/blue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

3

### 3.2. Licencia

Scratch y sus trabajos derivados son cubiertos por la licencia de código abierto AGPL-3.01¹⁰ (https://github.com/scratchfoundation/scratch-editor?tab=AGPL-3.0-1-ov-file)

### 3.3. Configuración inicial

Por conveniencia, se puede realizar un acceso directo al archivo index.htlm dentro de la carpeta scratch . Este archivo es el “ejecutable” de AttaScratch.

## 4. Interfaz de usuario

### 4.1. Pantalla principal

Sin importar la forma con la que se lanza AttaScratch, se abrirá el proyecto “plantilla.sb3”, como el de la fig.1, utilizado en el build de la aplicación. Al momento de finalizar el TFG, se dejó con un proyecto de ejemplo de seguidor de línea, dibujador de figuras y un pendant.


Figura 1: Pantalla Inicio AttaScratch

10https://github.com/scratchfoundation/scratch-editor?tab=AGPL-3. 0-1-ov-file (https://github.com/scratchfoundation/scratch-editor?tab=AGPL-3.0-1-ov-file)

4

### 4.2. Menús, barras de herramientas, accesos directos

Para aprender a usar y navegar Scratch, en la cinta superior se encuentra con una pestaña de tutoriales que explican y enseñan a utilizar Scratch mediante videos e instrucciones.

La extensión del AttaBot se encuentra de última en el listado de extensiones en el listillo izquierdo de la interfaz. Se resalta que los bloques de la extensión son solamente para su uso en Sprites.

El proyecto plantilla contiene comentarios que explican a más detalle aspectos de navegación e interacción en Scratch.

## 5. Operaciones básicas de AttaScratch

### 5.1. Cómo empezar un proyecto

En la cinta superior en la pestaña de Archivo se tiene las opciones de Nuevo (que abrirá el proyecto plantilla), Cargar y Guardar.

En términos de las funciones específicas de AttaScratch: Los bloques por defecto realizarán sus funciones del modo gráfico en el Sprite en el que se hayan colocado.

Para realizar la transmisión de los comandos al AttaBot-STEM, los bloques de la extensión (o un bloque función definido con bloques de la extensión) debe ser colocado dentro del bloque C Modo de transmisión de comandos al AttaBot para que en vez de realizar acciones gráficas, generen el string de comando de la secuencias. Por último el bloque Transmitir por BLE es el encargado de transmitir su argumento al AttaBot-STEM. Por defecto, la idea es utilizar de argumento el bloque variable string de comando, pero como el ejemplo del pendant demuestra, el bloque acepta cualquier variable de string, incluido el escribir directamente en el argumento. Un ejemplo se muestra en la fig. 2.

5


Figura 2: Envio de comandos al AttaBot

De querer o necesitar una explicación detallada de lo que realiza cada bloque, se puede revisar su código en el repositorio¹¹ (https://github.com/Jocaguz/AttaScratch/blob/master/your-scratch-extension/index.js) o el informe del TFG¹² (https://www.overleaf.com/read/tnjvyjqxwgbf#cfc726)

### 5.2. Entrada/carga de datos

AttaScratch puede abrir proyectos de Scratch oficial y proyectos generados por si mismo. Además se puede importar objetos de Scratch .sprite3 (lo cual incluye sus trajes y programación), imágenes vectoriales, mapas de bit entre otros formatos para ser utilizados de fondos o Sprites.

Además, mediante el bloque Importar de la APP AttaScratch puede abrir un archivo de guardado de la aplicación Android Atta-Bot App para generar los bloques equivalentes a la secuencia en el archivo.

### 5.3. Guardar y exportar

Los proyectos se guardan en archivos .sb3 que son comprimidos .zip codificados con todas la información de los objetos, fondos, gráficos y bloques colocados en un proyecto. También se puede exportar a archivos objeto Scratch individuales .sprite3 los cuales guardan los trajes y bloques colocados en ellos para ser utilizados en otros proyectos.

11https://github.com/Jocaguz/AttaScratch/blob/master/your-scratch-extension/index.js (https://github.com/Jocaguz/AttaScratch/blob/master/your-scratch-extension/index.js) 12https://www.overleaf.com/read/tnjvyjqxwgbf#cfc726

6

Además, mediante el bloque Exportar puede guardar una secuencia de comandos del AttaBot en un archivo .dat compatible con la aplicación Android Atta-Bot App.

## 6. Funcionalidades avanzadas

Este apartado se enfoca en el ambiente de desarrollo de AttaScratch.

### 6.1. Automatización, scripts, integraciones

El ambiente de desarrollo se basa en un contenedor de Docker. La idea del proyecto es trabajarlo en un codespace de GitHub, pero se puede realizar el setup local.

Una vez cargado el ambiente, se contará con un editor de Visual Studio Code. En la terminal del editor se debe ejecutar ./0-setup.sh, este archivo bash termina de configurar el ambiente y dependencias de Scratch.

El ambiente cuenta con 5 archivos bash de automatización:

./0-setup.sh: obtiene los repositorios de Scratch-vm y Scratch-gui ,y ejecuta los cambios indicados en los archivos de patch para cada uno de ellos.

./1-add-dependency.sh: se utiliza para agregar dependencias NPM a la extensión de Scratch que se esta desarrollando. Al momento de finalización del TFG, AttaScratch no utiliza ninguna dependencia.

./2-build.sh: construye la aplicación localmente en el Docker.

./3-run-private.sh: crea un servidor privado en el Docker para probar la aplicación que se ha creado.

./4-publish.sh: crea un fork gh-pages del master del repositorio. En este nuevo fork construye la aplicación y configura la página de Github pages para que realice el hosting.

La extensión como tal es el archivo index.js, aquí se define y programan los bloques. Para información detallada ver la documentación de Scratch VM¹³ (https://github.com/scratchfoundation/scratch-editor/blob/develop/packages/scratch-vm/docs/extensions.md) y

13https://github.com/scratchfoundation/scratch-editor/blob/develop/packages/scratch-vm/docs/extensions.md (https://github.com/scratchfoundation/scratch-editor/blob/develop/packages/scratch-vm/docs/extensions.md)

7

el asistente de AI de la documentación de Scratch-vm¹⁴ (https://deepwiki.com/scratchfoundation/scratch-vm)

Además, el aspecto visual de Scratch es manejado por Scratch-gui su documentación se encuentra aquí¹⁵ (https://github.com/scratchfoundation/scratch-editor/tree/develop/packages/scratch-gui) y también en DeepWiki con el asistente de AI¹⁶ (https://deepwiki.com/scratchfoundation/scratch-gui)

### 6.2. Personalización avanzada

Hay cuatro vectores de modificación de AttaScratch. La extensión en index.js, modificar Scratch-vm mediante el patch, modificar Scrtach-gui mediante el patch y modificar el proyecto resultante del build.

El modificar el index.js es simple. Directamente en el archivo index.js se agregan o modifican las lineas de código que definen los bloques.

El modificar Scratch-vm y Scratch-gui es más complicado e indirecto. Estos elementos se modifican mediante archivos .patch que son documentos de diferencia como los commits de git y github. Estos patch se realizan la primera vez que se ejecuta ./0-setup.sh sobre ellos y solo la primera vez. Si se requiere volver a aplicar los patch, se debe volver a inicializar los directorios de Scratch-vm y Scratch-gui con los originales. Mi forma de hacerlo es crear un nuevo codespace una vez que los patch hayan sido actualizados (git me estresa).

Modificar el proyecto resultante también es bastante simple. En el directorio de scratch (AttaScratch) se encuentran todas la imágenes, videos, códigos, binarios etc que el navegador utiliza para ejecutar y renderizar la aplicación. Entonces, por ejemplo se puede sencillamente abrir el logo de ”Scratch” y modificar (o sobrescribirlo con un archivo del mismo nombre) y cuando la aplicación se sirva/ejecute se observará el nuevo logo.

### 6.3. Exportación de aplicaciones HTLM

Una característica muy obviada es que Scratch es un IDE que crea aplicaciones web HTLM¹⁷. (https://scratch.mit.edu/explore/projects/all) Al crear un cliente de Scratch no oficial como AttaScratch

14https://deepwiki.com/scratchfoundation/scratch-vm15https://github.com/scratchfoundation/scratch-editor/tree/develop/packages/scratch-gui (https://github.com/scratchfoundation/scratch-editor/tree/develop/packages/scratch-gui)
16https://deepwiki.com/scratchfoundation/scratch-gui17https://scratch.mit.edu/explore/projects/all

8

se pierde el acceso automático a esta característica oficial. Para utilizarla se necesita utilizar herramientas de terceros.

HTMLifier es la primera.¹⁸ (https://sheeptester.github.io/htmlifier/) Esta herramienta se puede descargar para usarla offline o desde el sitio Web y la segunda es TurboWarp.¹⁹ (https://packager.turbowarp.org/) Este cliente no oficial de Scratch también cuenta con un packager para crear las aplicaciones HTLM. Ambas herramientas reciben proyectos .sb3 y crean los “ejecutables” de HTLM. También pueden utilizar extensiones no oficiales como la de AttaScratch para la compilación.

Nota: Para estas herramientas se le carga el proyecto .sb3 y un archivo index.js (la extensión). Sin embargo, al momento de terminar el TFG el index.js del AttaScratch no es compatible porque AttaScratch se crea desde el código fuente y por ende, sus “librerías incluidas” son literalmente los archivos de código de scratch-vm. Mientras que, HTMLifier y TurboWarp utilizan un motor de Scratch ya compilado que en el código de la extensión se llama Scratch.propiedad.

Para hacer compatible los proyectos AttaScratch con esta herramientas se necesita copiar el index.js y modificar las constantes de llamado de propiedades y utilidades para que utilicen el objeto Scratch. Se puede leer más al detalle aquí: Documentación de extensiones no oficiales de TurboWarp²⁰ (https://docs.turbowarp.org/development/extensions/introduction) .
En buena teoría con cambiar las definiciones const al inicio de la copia del index.js se lograría, pero falta probar y experimentar.

## 7. Problemas comunes

### 7.1. Errores frecuentes y soluciones

El cursor desaparece sobre bloques u otros objetos: Ir a configuración del navegador y apagar “aceleración por hardware” / “aceleración gráficos por hardware”.

Los bloques se separan de los valores de sus parámetros: Ir a archivo, guardar, darle F5 y cargar al proyecto. Es un bug puramente visual de cuando el shadowblock de la GUI no se asigna correctamente a su

18https://sheeptester.github.io/htmlifier/19https://packager.turbowarp.org/20https://docs.turbowarp.org/development/extensions/introduction

9

bloque padre.

Al intentar de publicar con el ./4-publish.sh retorna que no hay cambios: ir a una linea de comentario del index.js y darle a la tecla espacio. Mientras index.js se vea anaranjado en el control de cambios, volver a ejecutar ./4-publish.sh.

### 7.2. Preguntas frecuentes (FAQ)

Se conocerán cuando hayan usuarios frecuentes

## 8. Soporte y recursos

### 8.1. Contacto técnico

Autor de AttaScratch: jc.gutierrez.z@outlook.com

### 8.2. Enlaces a documentación adicional

El código fuente de este manual se encuentra aquí²¹, (https://www.overleaf.com/read/vygmzbxxgspj#2888ad) para que se pueda utilizar de base y/o se actualice como sea necesario. Pueden descargarlo o realizar una copia.

21https://www.overleaf.com/read/vygmzbxxgspj#2888ad

10

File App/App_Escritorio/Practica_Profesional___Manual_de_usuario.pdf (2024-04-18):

# Instituto Tecnológico de Costa Rica

## Escuela de Computación Ingeniería en Computación Practica profesional

Manual de usuario

## Simplificación de los Atta-Bots para un entorno educativo

## Estudiante:

2018189196 - Isaac David Ortega Arguedas

Fecha de entrega: 7 de Junio, 2023

## I semestre 2023

## Índice

1. Introducción | 2
2. Instalación | 2
3. Ejecución de la aplicación | 4
4. Utilización del programa | 4
5. Desinstalar la aplicación | 14
6. Conclusión | 15

1

## 1. Introducción

El presente documento es el manual de usuario del programa que será entregado por Isaac David Ortega Arguedas, como proyecto de la Practica Profesional para el primer semestre del 2023, a los miembros de investigación PROE, esto es para que tengan material de referencia en caso de tener alguna duda sobre el programa. Este manual va a cubre todos los pasos necesarios para el correcto uso de la aplicación incluyendo el proceso de instalación.

## 2. Instalación

Para instalar la aplicación solo se requiere ejecutar el instalador (ver Figura 1).

Figura 1: Instalador de Atta-Bots-Kids

Una vez ejecutemos el instalador se nos abrirá una ventana (ver Figura 2) en la cual se nos indica que indicara los pasos necesarios para instalar la aplicación. Para proseguir con la instalación pulsamos el botón ”Next”.


Figura 2: Confirmar que se quiere instalar la aplicación

En el segundo paso es para indicar donde deseamos instalar la aplicación, así como indicar si deseamos que la aplicación se instale para todos los usuarios de la computadora o solo para el usuario en el que nos encontramos actualmente (ver Figura 3). Ya se cuenta con una dirección por defecto, pero es si se desea cambiar dicha dirección es posible pulsando el botón ”Browse...”. Una vez hayamos escogido la dirección deseada, así como a quienes deseamos instalar la aplicación pulsamos el botón ”Next”.

2


Figura 3: Se escoge donde se desea instalar la aplicación

Una vez pulsado se nos abrirá una ultima ventana la cual es de confirmación (ver Figura 4). Si estamos seguro de las opciones escogidas en la ventana anterior pulsamos ”Next”, de los contrario podemos pulsar ”Back”para regresar a la ventana anterior. En caso de que deseemos proseguir, se nos abrirá una ventana de Windows preguntando si estamos seguros de querer instalar la aplicación, aceptamos la instalación.


Figura 4: Confirmar opciones

3

Cuando la instalación haya finalizado se nos abrirá una ultima ventana la cual nos indica que la instalación se realizó correctamente (ver Figura 5). Aquí solo debemos pulsar ”Close”.


Figura 5: Mensaje de instalación

Para este punto si nos dirigimos al escritorio podemos observar que apareció una nueva aplicación (ver Figura 6).

Figura 6: Icono de la aplicación

## 3. Ejecución de la aplicación

La ejecución de esta aplicación es igual que cualquier otra.

## 4. Utilización del programa

En esta sección se explicará en detalle todas las funcionalidades con las que cuenta esta aplicación. Se explicará qué acción realiza cada función así como la forma en la que se espera que el usuario interactúe.

### 4.1. Avanzar

El botón que representa esta función (ver Figura 7) es el siguiente.

4

Figura 7: Botón Avanzar

La funcionalidad que cumplen es la de hacer que el Atta-Bot, se mueva hacia adelante. Al momento de interactuar con el botón, una nueva ventana (ver Figura 8) se abrirá. En esta ventana el usuario le indica al sistema cuántos milímetros desea que el Atta-Bot se mueva hacia adelante.


Figura 8: Cuadro de confirmación avanzar

La forma en la cual el usuario escoge la cantidad de milímetros a avanzar es mediante el slider. Si pulsamos el botón “Ok”, el sistema almacenará la información, se agregará al historial y, cuando se le indique a la aplicación, esta será cargada al Atta-Bot, en caso de que pulse el botón “Cancelar” no pasara nada y se cerrará esta ventana. Lo mínimo que puede avanzar el Atta-Bot son 50 milímetros y el máximo son 999 milímetros.

### 4.2. Retroceder

El botón que representa esta función (ver Figura 9) es el siguiente.

5

Figura 9: Botón Retroceder

La funcionalidad que cumplen es la de hacer que el Atta-Bot, se mueva hacia atrás. Al momento de interactuar con el botón, una nueva ventana (ver Figura
10) se abrirá. En esta ventana el usuario le indica al sistema cuántos milímetros desea que el Atta-Bot se mueva hacia atrás.


Figura 10: Cuadro de confirmación retroceder

La forma en la cual el usuario escoge la cantidad de milímetros a retrocer es mediante el slider. Si pulsamos el botón “Ok”, el sistema almacenará la información, se agregará al historial y, cuando se le indique a la aplicación, esta será cargada al Atta-Bot, en caso de que pulse el botón “Cancelar” no pasara nada y se cerrará esta ventana. Lo mínimo que puede retroceder el Atta-Bot son 50 milímetros y el máximo son 999 milímetros.

### 4.3. Girar a la izquierda

El botón que representa esta función (ver Figura 11) es el siguiente.

Figura 11: Botón Girar a la Izquierda

La funcionalidad que cumple es la de hacer que el Atta-Bot gire hacia la izquierda. Al momento de interactuar con alguno el botón aparecerá una nueva ventana (ver Figura 12). En esta ventana el usuario le indica al sistema cuántos grados desea que el Atta-Bot gire a la izquierda.

6

Figura 12: Cuadro de confirmación girar a la izquierda

Si pulsamos el botón “Ok”, el sistema almacenará la información, se agregará al historial y, cuando se le indique a la aplicación, esta será cargada al Atta-Bot, en caso de que pulse el botón “Cancelar” no pasara nada y se cerrará esta ventana. El robot es capaz de hacer giros de 360°, motivo por el cual este es el máximo que puede girar.

### 4.4. Girar a la derecha

El botón que representa esta función (ver Figura 13) es el siguiente.

Figura 13: Botón Girar a la Derecha

La funcionalidad que cumple es la de hacer que el Atta-Bot gire hacia la derecha. Al momento de interactuar con alguno el botón aparecerá una nueva ventana (ver Figura 14). En esta ventana el usuario le indica al sistema cuántos grados desea que el Atta-Bot gire a la derecha.

Figura 14: Cuadro de confirmación girar a la derecha

Si pulsamos el botón “Ok”, el sistema almacenará la información, se agregará al historial y, cuando se le indique a la aplicación, esta será cargada al Atta-Bot, en caso de que pulse el botón “Cancelar” no pasara nada y se cerrará esta ventana. El robot es capaz de hacer giros de 360°, motivo por el cual este es el máximo que puede girar.

7

### 4.5. Activar ciclo

El botón que representa esta función (ver Figura 15) es el siguiente.

Figura 15: Botón Ciclo

La funcionalidad que cumple es que, una vez se haya activado, todas las instrucciones posteriores serán ejecutadas de forma reiterativa. Para facilitar la comprensión de esto, las instrucciones subsecuentes aparecerán más hacia el centro del historial que las instrucciones que no se encuentren dentro del ciclo. Cuando se interactúa con este botón aparecerá una nueva ventana preguntando si deseamos activar un ciclo (ver Figura 16), si se pulsa “Ok” este se activará y el icono cambiará, si se pulsa “Cancelar”, solo se cerrará la ventana.


Figura 16: Cuadro de confirmación agregar ciclo

Una vez el ciclo es activado, la apariencia del botón cambia (ver Figura 17). Esto también es para indicar que el ciclo esta activo.

Figura 17: Botón apagado de Ciclo

Si se pulsa nuevamente sobre el botón aparecerá una nueva ventana la cual preguntará si se desea quitar el ciclo (ver Figura 18). Si pulsamos “Ok” las instrucciones que se hayan agregado después de haberlo activado se moverán a la posición normal y el icono regresará al original. Esto permite mover el ciclo a un punto posterior en la secuencia de instrucciones.

8


Figura 18: Cuadro de confirmación quitar ciclo

### 4.6. Detectar obstáculo

El botón que representa esta función (ver Figura 19) es el siguiente.

Figura 19: Botón Obstáculo

La funcionalidad que cumple es que una vez se haya activado el Atta-Bot se detendrá cuando detecte un obstáculo. Cuando se interactúa con este botón aparecerá una nueva ventana preguntando si deseamos detectar obstáculos (ver Figura 20). Si se pulsa “Ok” este se activará y el icono cambiará, si se pulsa “Cancelar”, solo se cerrará la ventana.

Figura 20: Cuadro de confirmación activar detección obstáculos

Una vez la detección de obstáculos es activada, la apariencia del botón cambia (ver Figura 21). Esto con el fin de recordarle al usuario que la detección de obstáculos esta activado.

9

Figura 21: Botón apagado de Obstáculo

Si se pulsa nuevamente sobre el botón aparecerá una nueva ventana la cual preguntará si se desea dejar de detectar obstáculos (ver Figura 22). Si pulsamos “Ok” el Atta-Bot no detendrá la ejecución de las instrucciones cargadas a menos que se le detenga de forma manual, o que haya ejecutado todas las instrucciones cargadas, y el icono regresará al original.


Figura 22: Cuadro de confirmación desactivar detección obstáculos

### 4.7. Cargar instrucciones

El botón que representa esta función (ver Figura 23) es el siguiente.

Figura 23: Botón Play

La funcionalidad que cumple es la de cargar las instrucciones que se encuentren en el historial al Atta-Bot. Cuando se interactúa con este botón aparecerá una nueva ventana preguntando si deseamos cargar las instrucciones (ver Figura 24), si se pulsa “Ok” las instrucciones se cargan al Atta-Bot y este las empezará a ejecutar, si se pulsa “Cancelar”, solo se cerrará la ventana.

10


Figura 24: Cuadro de confirmación cargar código

### 4.8. Detener ejecución

El botón que representa esta función (ver Figura 25) es el siguiente.

Figura 25: Botón Stop

La funcionalidad que cumple es la de detener al Atta-Bot, sin importar qué acción esté realizando. Cuando se interactúa con este botón aparecerá una nueva ventana preguntando si deseamos detener al Atta-Bot (ver Figura 26), si se pulsa “Ok” el Atta-Bot se detendrá, si se pulsa “Cancelar”, solo se cerrará la ventana.

Figura 26: Cuadro de confirmación detener ejecución

### 4.9. Borrar una instrucción en específico

Al momento de agregar nuevas instrucciones estas van a ser representadas de una forma similar a la Figura 27. Si se hace click sobre el botón la instrucción que está relacionada con dicho botón será borrada del historial sin preguntar por ningún tipo de confirmación.

11

Figura 27: Ejemplo de instrucciones en el historial

### 4.10. Limpiar historial

Esta acción puede realizarse mediante dos formas. La primera es pulsando el botón que se asemeja a un basurero (ver Figura 28).

Figura 28: Botón Limpiar

La otra forma es mediante el menú. Primero hacemos click sobre .Archivo ² posteriormente pulsamos ”Limpiar Historial”tal y como se ejemplifica en la Figura 29.

Figura 29: Opción para limpiar el historial

Una vez se haya interactuado de alguna de las dos maneras mencionadas, aparecerá una nueva ventana preguntando si deseamos borrar el historial (ver Figura 30). En caso de pulsar “Ok” las instrucciones del historial se borrarán y, si se llegaron a activar, las opciones de ciclo y detectar obstáculos se desactivaran, si se pulsa “Cancelar”, solo se cerrará la ventana.

12


Figura 30: Cuadro de confirmación borrar historial

### 4.11. Generar documento

Esta función se representa de la siguiente forma (ver Figura 31).

Figura 31: Opción generar documento

La funcionalidad que cumple es la de generar un documento el cual cuente con las instrucciones que se encuentren en el historial en ese momento. Cuando se interactúa con este botón aparecerá una nueva ventana en la cual indicamos donde deseamos guardar el archivo de texto(.txt) y el nombre de dicho archivo (ver Figura 32).


Figura 32: Seleccionar donde guardar el documento a generar

Si pulsamos “Guardar”se creará un nuevo archivo el cual almacena las instrucciones que se encuentren en el historial. En el caso de que ya exista un archivo de texto con el mismo nombre en el lugar donde se desea guardar, el programa preguntará si se desea sobreescribir el archivo. Por el contrario, si se pulsa “Cancelar” no ocurrirá nada.
La forma en la que las instrucciones se representan en el documento que se acaba de crear es mediante tres letras que representan la instrucción a realizar seguidas por un guión y, después de este guión, se encuentra una secuencia

13 numérica de 1 a 3 dígitos de largo. Las abrebiaciones y se respectiva instrucción son las siguientes: del de delante representa avanzar; atr es para atrás (retroceder); izq de izquierda y der de derecha; obs es para los obstáculos, si el numero que lo acompaña es 0 es que no los detecta, si es 1 sí los detecta; rep de repetir es para indicar el ciclo.

### 4.12. Versión

Esta función se representa de la siguiente forma (ver Figura 33).

Figura 33: Opción versión de la aplicación

Indica la versión actual de la aplicación en una nueva ventana. La ventana es similar a la figura 34.


Figura 34: Versión de la aplicación

### 4.13. Ayuda

Esta función se representa de la siguiente forma (ver Figura 35).

Figura 35: Opción ayuda

Redirige al usuario al manual de usuario, en otras palabras el documento que esta leyendo actualmente.

## 5. Desinstalar la aplicación

Para desinstalar la aplicación, debemos ejecutar el instalador (ver Figura 36). Escogemos la opción para remover la aplicación y pulsamos ”Finish”.

14


Figura 36: Mensaje de instalación

## 6. Conclusión

Este programa facilita modificar el comportamiento de los Atta-Bots. Ayudando a su vez a enseñar los principios de la programación de una forma simplificada para que de esta forma eventualmente estos conocimientos se puedan expandir.

15

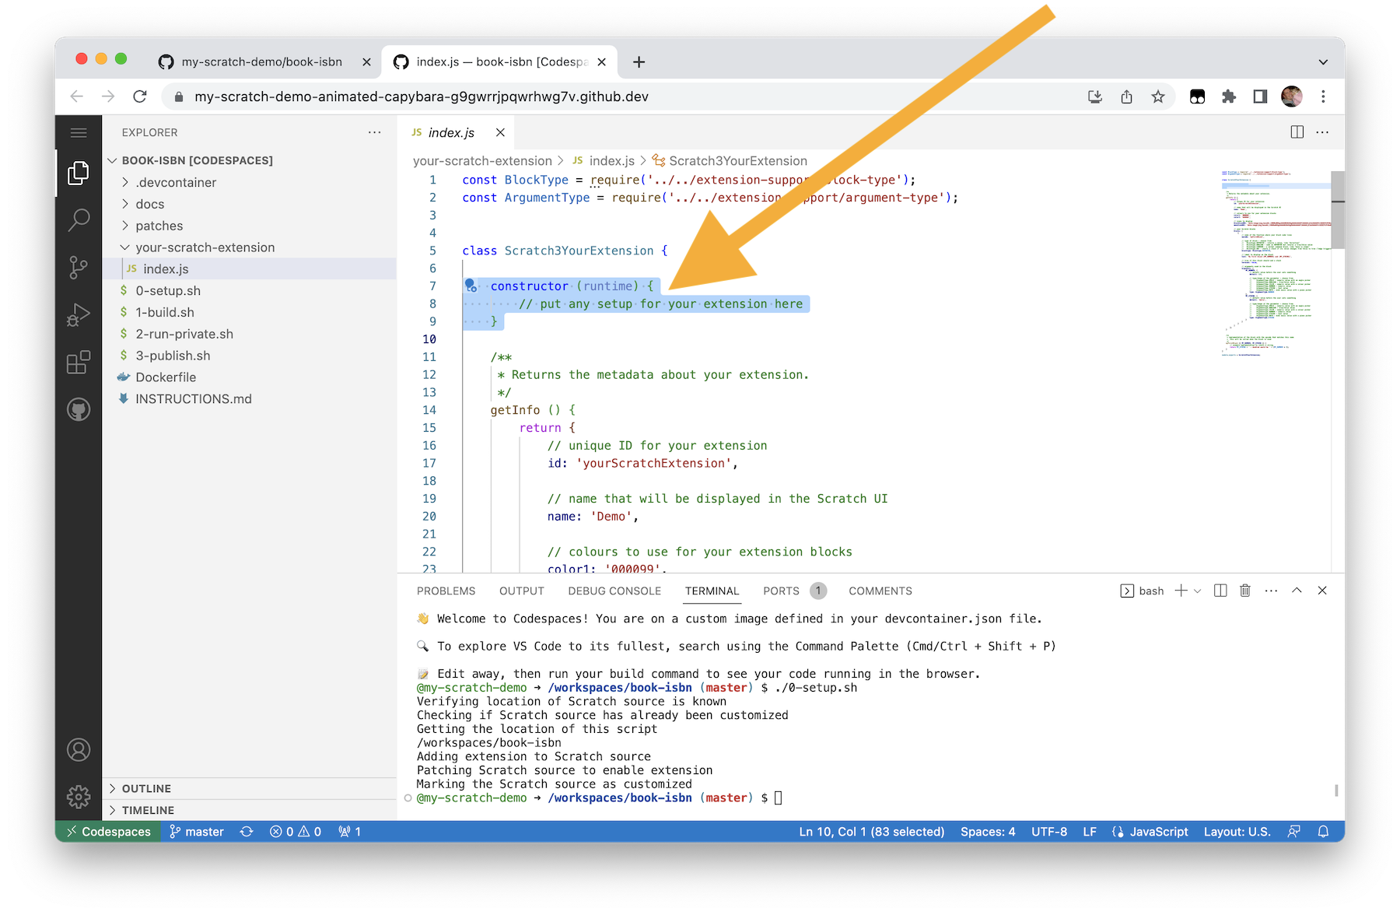
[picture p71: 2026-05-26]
AttaScratch/docs/41-constructor.png

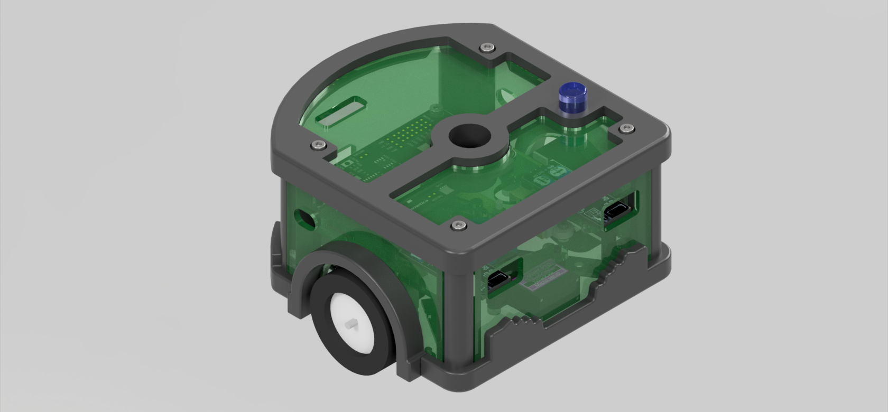
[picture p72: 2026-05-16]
Chasis/2. Archivos Para Impresión/Renders/Ensamble_completo.png

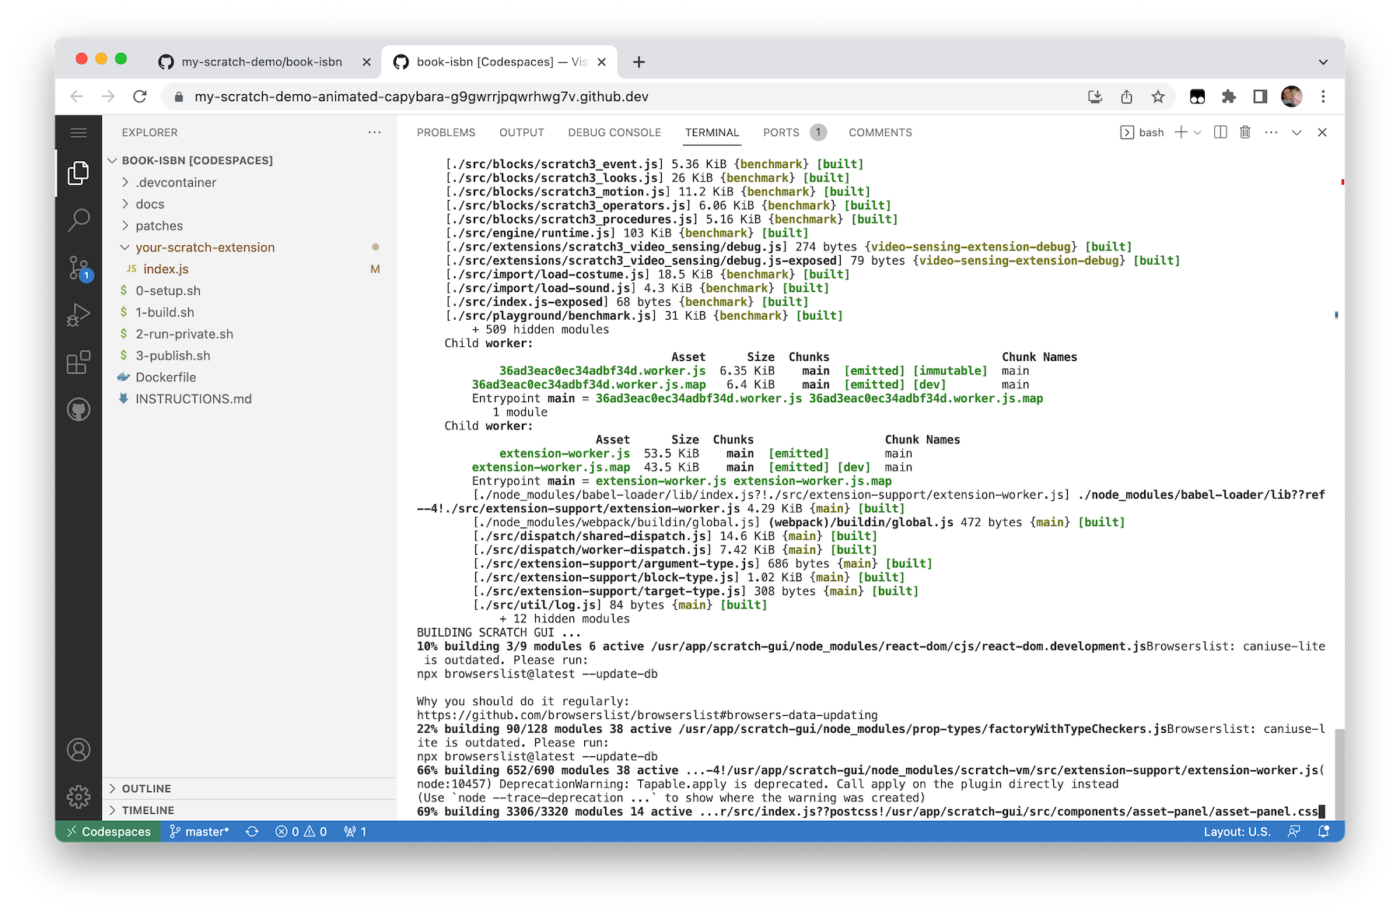
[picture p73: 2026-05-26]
AttaScratch/docs/51-building.png

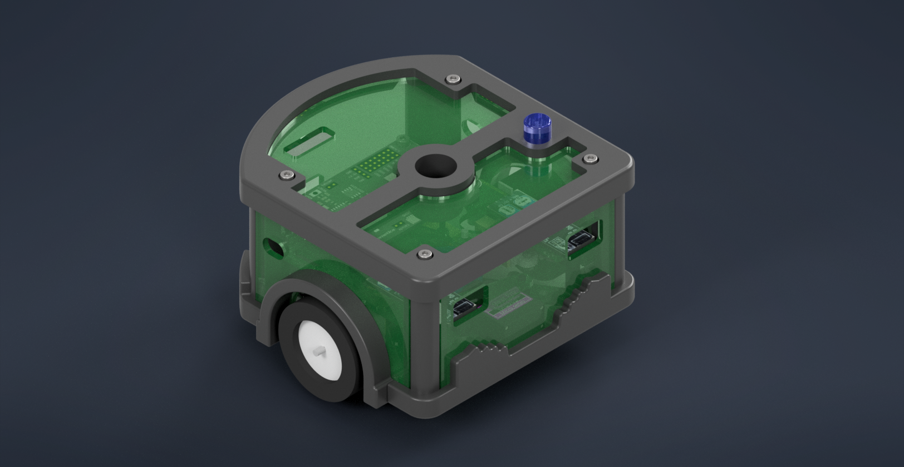
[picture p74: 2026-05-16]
Chasis/2. Archivos Para Impresión/STL/Renders/Ensamble_completo.png

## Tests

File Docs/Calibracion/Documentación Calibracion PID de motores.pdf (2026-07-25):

## Documentación: Calibración de PID de motores Atta-Bot

## STEM

- Documentos y recursos de referencia

CalibracionMotores.ino — firmware para la medición de Pulsos por Revolución (PPR) de cada motor mediante los encoders.
PID_Values.xlsx — bitácora de valores de PPR medidos y de constantes PID probadas por robot, con el resultado ("Pasa"/"Falla") de cada prueba.

### 1. Medición de PPR de cada motor

El primer paso consiste en cargar el firmware CalibracionMotores.ino en el robot y medir el PPR real de cada motor (derecho e izquierdo) por separado.

### 1.1 Procedimiento

1. Cargar el firmware CalibracionMotores.ino en el microcontrolador del robot.
2. Colocar el acrílico (brazo) de calibración en el eje del motor que se va a medir.
3. Abrir el Monitor Serial a 115200 baudios.
4. Enviar el comando "medirDerecho" para iniciar la medición del motor derecho, o "medirIzquierdo" para el motor izquierdo.
5. Esperar a que el firmware realice automáticamente las 10 mediciones configuradas, el sistema arranca el motor, mide el número de pulsos hasta el tope del brazo, descarta lecturas menores o iguales a PPRminimo, y muestra cada valor por el Monitor Serial.
6. Registrar el promedio de PPR que el firmware imprime al finalizar la última medición.
7. Enviar el comando "reset" para detener el motor y reiniciar los contadores antes de calibrar el siguiente motor o de repetir una medición.
8. Repetir el proceso con el segundo motor del mismo robot.

### 1.2 Criterio de aceptación

La diferencia entre el PPR promedio del motor derecho y el del motor izquierdo debe ser de máximo ±10 PPR. Este margen asegura que el promedio de ambos motores represente de forma precisa el comportamiento real del robot.

Motor fuera de rango:

Si la diferencia entre ambos motores supera ±10 PPR, se debe sustituir el motor que presente la desviación y repetir la medición de PPR para el motor nuevo antes de continuar con el paso 2.

### 1.3 Registro de resultados

Los valores de PPR obtenidos para cada motor y robot se registran en la hoja "PPRs" del archivo PID_Values.xlsx, indicando el número de motor (cuando aplique) y el robot correspondiente. Este registro permite dar seguimiento histórico y ubicar rápidamente en qué rango de PPR se encuentra cada robot para el paso siguiente.

### 2. Selección de las constantes PID según el PPR

Una vez colocados los motores validados en el robot, se seleccionan las constantes Kp, Ki y Kd de referencia según el rango de PPR promedio medido, con base en las pruebas de prueba y error e investigación previa registradas en la hoja "PID" de PID_Values.xlsx.

Rango de PPR | Kp | Ki | Kd | Velocidad objetivo de referencia | Observaciones
500 – 600 | 1.0 | 2.5 | 0 | 120 | Caso ideal validado (Robot Gamma, PPR ≈ 584–590)

Rango de PPR | Kp | Ki | Kd | Velocidad objetivo de referencia | Observaciones
800 – 900 | 0.8 | 2.1 | 0 | 120 | Validado (Robot Alfa, PPR ≈ 825–827); Kp = 0.65–0.85 e Ki = 2.1–2.5

Rango recomendado para Kp:
Según la investigación previa registrada, la ganancia proporcional (Kp) debe mantenerse entre 0.75 y 1.1. Valores de Kp fuera de este rango han mostrado fallas en las pruebas.

Estos valores son un punto de partida; deben verificarse siempre con la prueba real del robot descrita en el paso 3, ya que corresponden a resultados empíricos y no a un modelo analítico cerrado.

### 3. Validación de las constantes PID

- Solamente si se cuenta con un PID Tuner completamente funcional, utilizarlo primero para obtener o refinar una propuesta de Kp, Ki y Kd antes de probar en el robot.
- Cargar las constantes seleccionadas (paso 2 o resultado del PID Tuner) en el firmware de control del robot.
- Ejecutar el robot a la velocidad objetivo (TargetSpeed) de prueba y observar la respuesta: tiempo de estabilización, presencia de sobreimpulso (overshoot) u oscilaciones sostenidas.
- Registrar el resultado de la prueba ("Pasa" o "Falla") junto con los valores de Kp, Ki, Kd y la velocidad objetivo, utilizada en la hoja "PID" de PID_Values.xlsx.

### 4. Diagnóstico en caso de que la calibración falle

Si la respuesta del robot no es satisfactoria ("Falla") con las constantes seleccionadas, seguir este orden de verificación antes de continuar probando combinaciones de Kp, Ki y Kd:

- Repetir la medición de PPR de ambos motores (paso 1) y confirmar que la diferencia sigue dentro de ±10 PPR; una medición inicial incorrecta invalida la selección de PID del paso 2.
- Recalibrar y volver a probar las constantes PID (paso 2 y 3) con el PPR confirmado.
- Si el problema persiste, revisar el robot de forma mecánica por posibles causas incluyen falta de lubricación, atascos en el tren motriz o en las ruedas, o fallo general de alguno de los motores.
- Sustituir el componente defectuoso identificado y reiniciar el procedimiento desde el paso 1.

### 5. Registro y control de resultados

Todo resultado de calibración (PPR y PID) debe quedar documentado en PID_Values.xlsx para mantener trazabilidad entre robots y evitar repetir pruebas ya descartadas. Cada nueva fila de prueba debe incluir el robot, las constantes utilizadas, la velocidad objetivo y el resultado obtenido.

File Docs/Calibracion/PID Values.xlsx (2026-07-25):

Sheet: PID
 |  | Caso ideal | Kp | Ki | Kd | TargetSpeed
Robot | Gamma | PID Actual | 1 | 2.5 | 0 | 120
Robot | Gamma |  | Kp | Ki | Kd | TargetSpeed | Pasa/Falla | Robot | Eduardo |  | Kp | Ki | Kd | TargetSpeed | Pasa/Falla
 |  | PID 1 | 1 | 2.5 | 0 | 180 | Falla |  |  | PID 1 | 0.75 | 2.5 | 0 | 120 | Falla
 |  | PID 2 | 1 | 2.5 | 0 | 140 | Pasa |  |  | PID 2 | 0.85 | 2.3 | 0 | 120 | Falla
 |  | PID 3 |  |  |  |  |  |  |  | PID 3 | 0.65 | 2.5 | 0 | 120 | Falla
 |  | PID 4 |  |  |  |  |  |  |  | PID 4 | 0.8 | 2.1 | 0 | 120 | Falla
 |  | PID 5 |  |  |  |  |  |  |  | PID 5 | 0.75 | 2.3 | 0 | 120 | Falla
 |  | PID 6 |  |  |  |  |  |  |  | PID 6
 |  | PID 7 |  |  |  |  |  |  |  | PID 7
 |  | PID 8 |  |  |  |  |  |  |  | PID 8
 |  | PID 9 |  |  |  |  |  |  |  | PID 9
 |  | PID 10 |  |  |  |  |  |  |  | PID 10
Robot | Alfa |  | Kp | Ki | Kd | TargetSpeed | Pasa/Falla
 |  | PID 1 | 1 | 2.5 | 0 | 120 | Falla
 |  | PID 2 | 0.82 | 2.3 | 0 | 120 | Pasa
 |  | PID 3 | 0.8 | 2.1 | 0 | 120 | Pasa
 |  | PID 4
 |  | PID 5
 |  | PID 6
 |  | PID 7
 |  | PID 8
 |  | PID 9
 |  | PID 10

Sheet: PPRs
Robot | #. Motor | Motor R | #. Motor | Motor L
Gamma |  | 584 |  | 590
Eduardo | 3 | 849.3 | F | 848
Alfa | 19 | 827.4 | E | 825.5
Robot | #. Motor | Motor R | #. Motor | Motor L
Eduardo |  | 874 |  | 868

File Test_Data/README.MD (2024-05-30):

Test data from validation and experiments

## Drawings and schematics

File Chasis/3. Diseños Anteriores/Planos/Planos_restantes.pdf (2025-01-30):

4 | 1 3 | 2

E

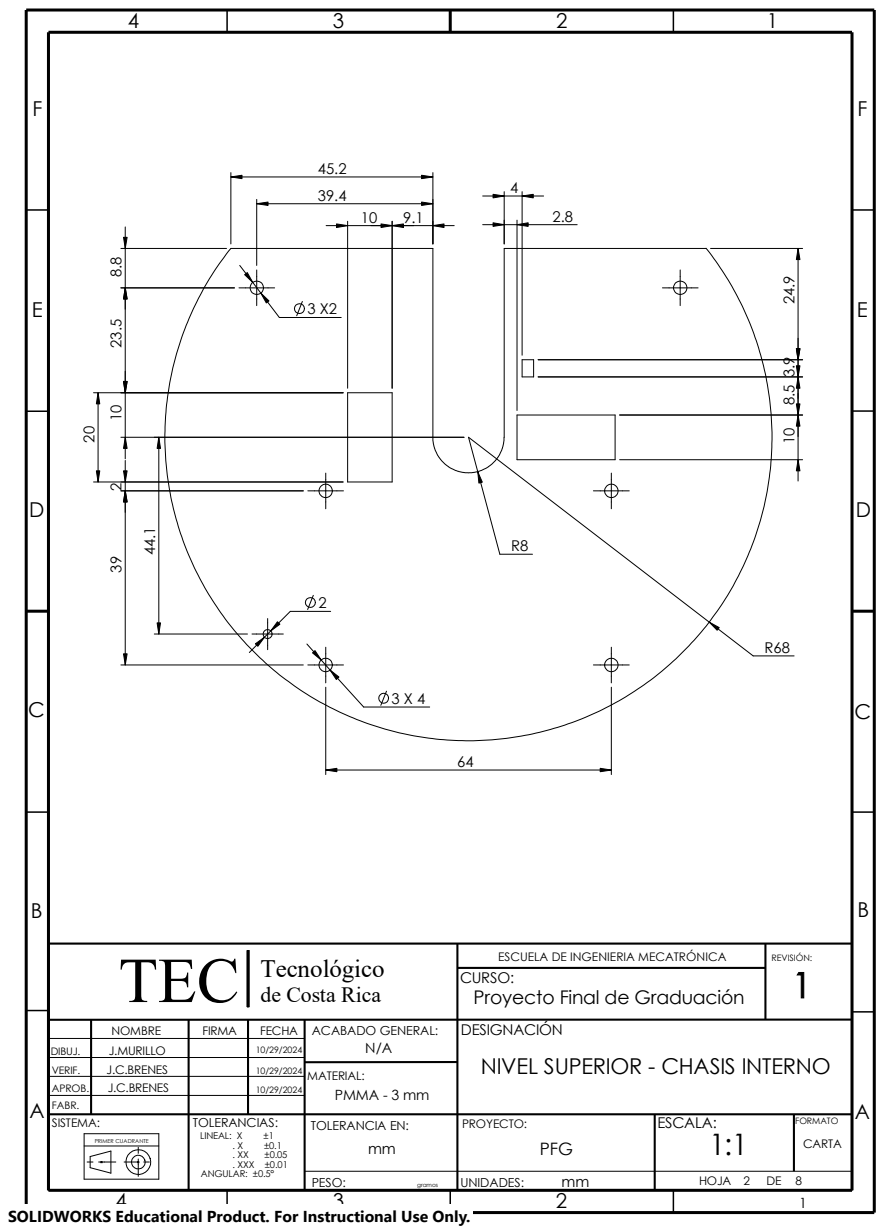
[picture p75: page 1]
Tecnológico TEC; PRIMER CUADRANTE; PMMA - 3 mm; REVISIÓN:; MATERIAL:

ESCUELA DE INGENIERIA MECATRÓNICA
CURSO:
Proyecto Final de Graduación

de Costa Rica

NOMBRE | FIRMA | FECHA | ACABADO GENERAL: N/A | DESIGNACIÓN NIVEL SUPERIOR - CHASIS INTERNO

DIBUJ. | J.MURILLO | | 10/29/2024
VERIF. | J.C.BRENES | | 10/29/2024
APROB. | J.C.BRENES | | 10/29/2024
FABR.
SISTEMA: | | | TOLERANCIAS: LINEAL: X ±1 . X ±0.1 . XX ±0.05 . XXX ±0.01 ANGULAR: ±0.5° | TOLERANCIA EN: mm | PFG | ESCALA: 1:1 | FORMATO PROYECTO: CARTA

PESO: gramos | mm UNIDADES: | HOJA 2 DE 8

SOLIDWORKS Educational Product. For Instructional Use Only.

E

F

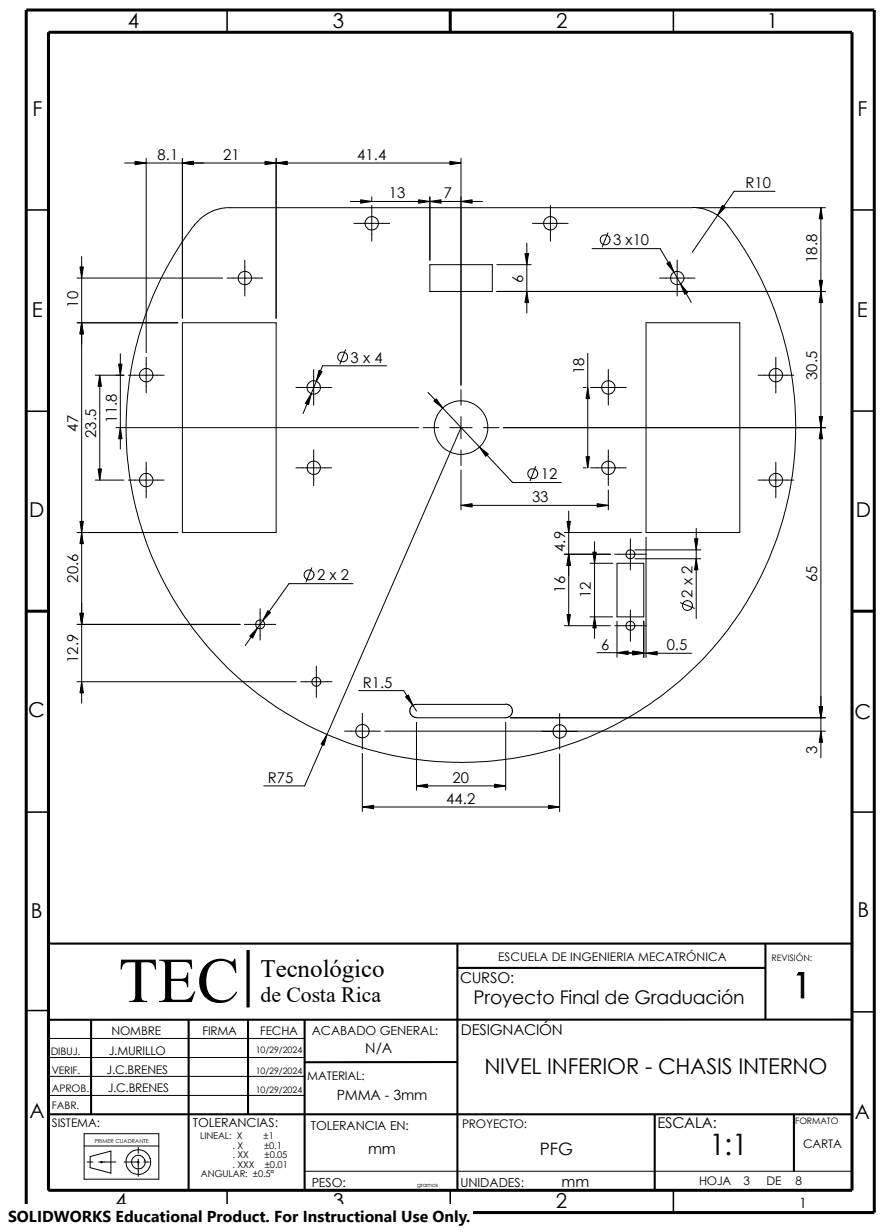
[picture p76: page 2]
Tecnológico TEC; PMMA - 3mm; REVISIÓN:; MATERIAL:

ESCUELA DE INGENIERIA MECATRÓNICA
CURSO:
Proyecto Final de Graduación

de Costa Rica

NOMBRE | FIRMA | FECHA | ACABADO GENERAL: N/A | DESIGNACIÓN NIVEL INFERIOR - CHASIS INTERNO

DIBUJ. | J.MURILLO | | 10/29/2024
VERIF. | J.C.BRENES | | 10/29/2024
APROB. | J.C.BRENES | | 10/29/2024
FABR.
SISTEMA: | | | TOLERANCIAS: | TOLERANCIA EN: | | ESCALA: 1:1 | FORMATO PROYECTO:

E

F

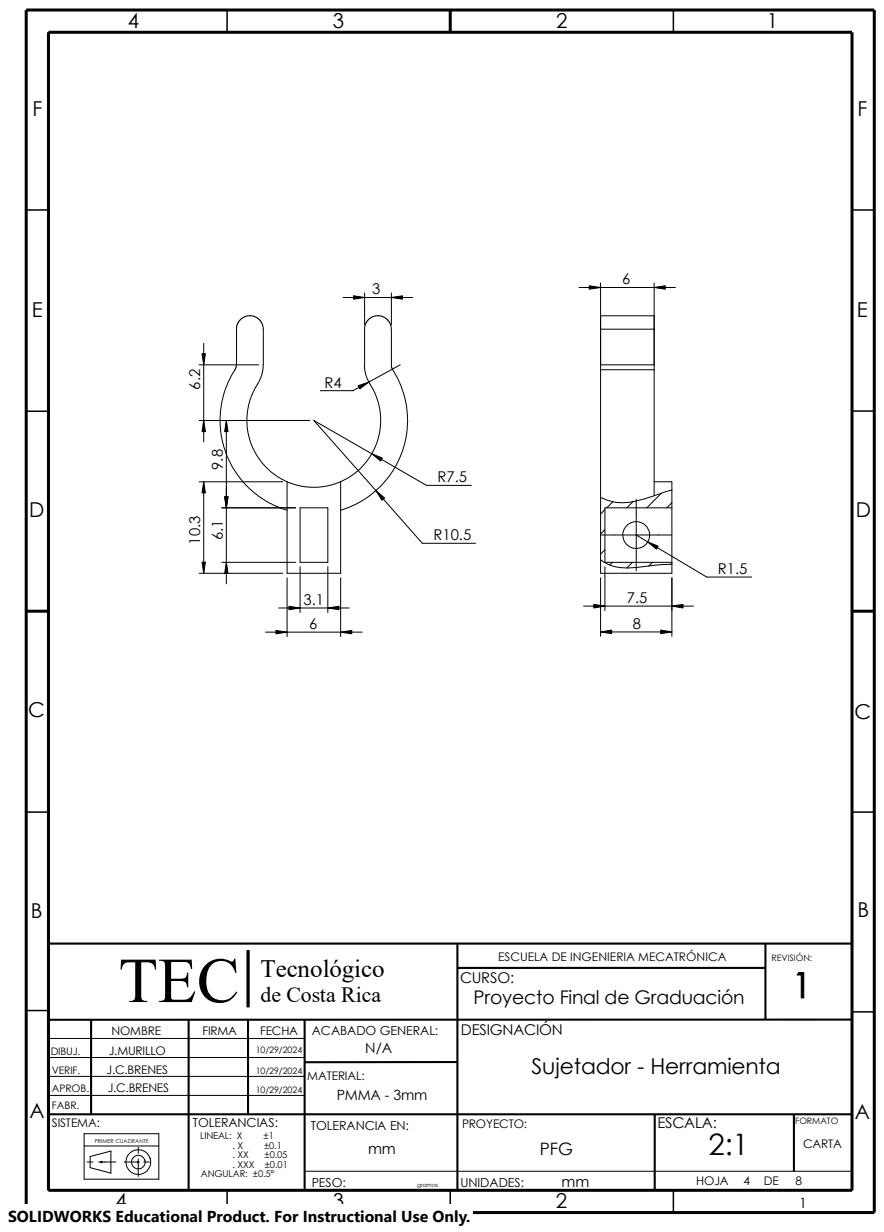
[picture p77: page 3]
Tecnológico TEC; PMMA - 3mm; REVISIÓN:; MATERIAL:

ESCUELA DE INGENIERIA MECATRÓNICA
CURSO:
Proyecto Final de Graduación

de Costa Rica

NOMBRE | FIRMA | FECHA | ACABADO GENERAL: N/A | DESIGNACIÓN Sujetador - Herramienta

DIBUJ. | J.MURILLO | | 10/29/2024
VERIF. | J.C.BRENES | | 10/29/2024
APROB. | J.C.BRENES | | 10/29/2024
FABR.
SISTEMA: | | | TOLERANCIAS: | TOLERANCIA EN: | | ESCALA: 2:1 | FORMATO PROYECTO:

18

E

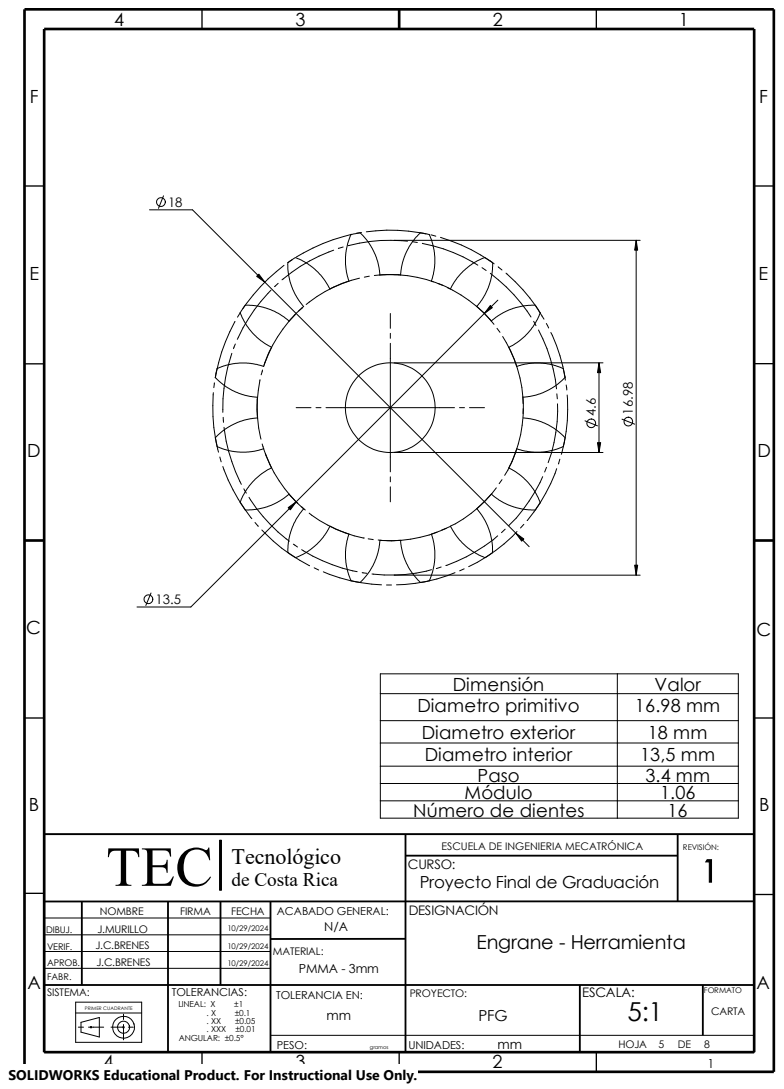
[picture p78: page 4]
Tecnológico TEC; PMMA - 3mm; REVISIÓN:; MATERIAL:; Diametro exterior; Número de dientes

Dimensión | Valor
Diametro primitivo | 16.98 mm

Diametro interior | 13,5 mm
Paso | 3.4 mm
Módulo | 1.06

ESCUELA DE INGENIERIA MECATRÓNICA
CURSO:
Proyecto Final de Graduación

de Costa Rica

NOMBRE | FIRMA | FECHA | ACABADO GENERAL: N/A | DESIGNACIÓN Engrane - Herramienta

DIBUJ. | J.MURILLO | | 10/29/2024
VERIF. | J.C.BRENES | | 10/29/2024
APROB. | J.C.BRENES | | 10/29/2024
FABR.
SISTEMA: | | | TOLERANCIAS: | TOLERANCIA EN: | | ESCALA: 5:1 | FORMATO PROYECTO:

E

F

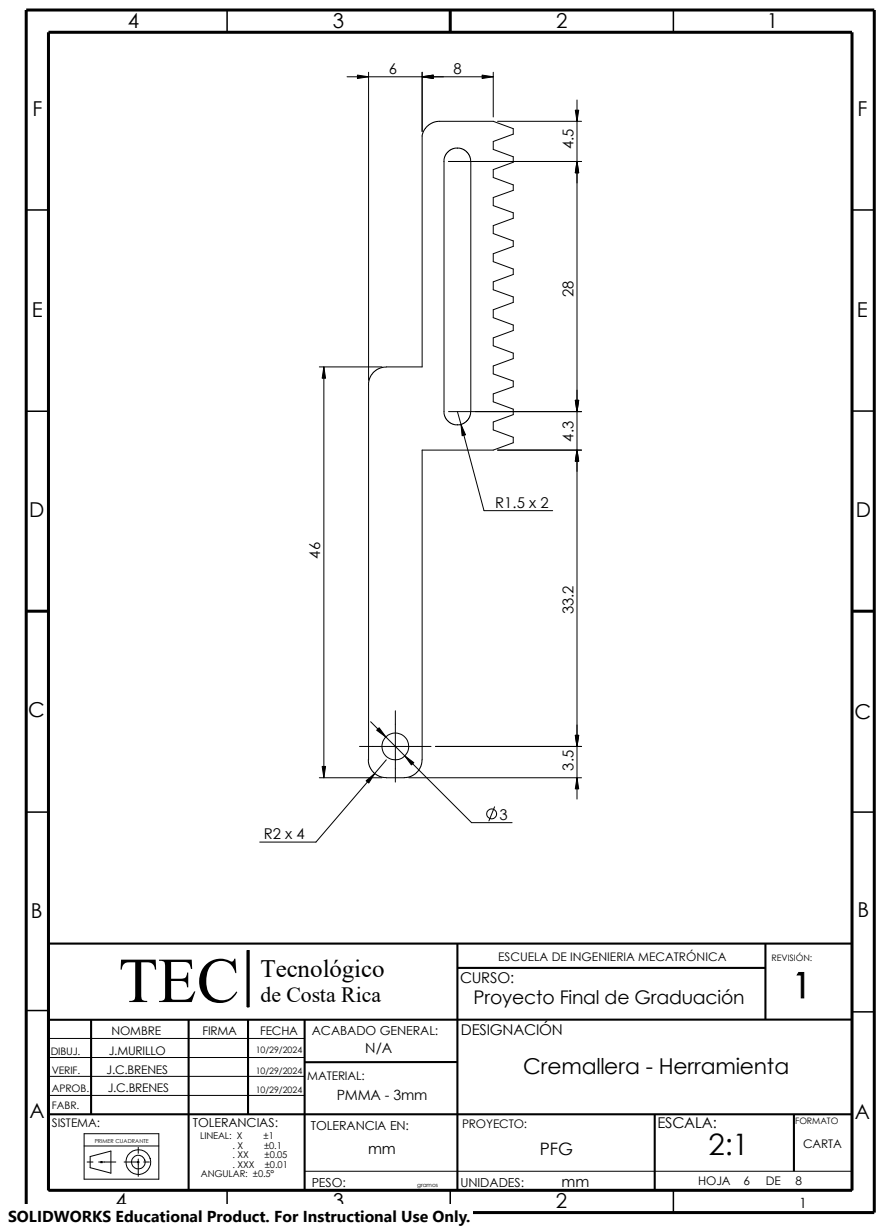
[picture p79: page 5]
Tecnológico TEC; PMMA - 3mm; REVISIÓN:; MATERIAL:

ESCUELA DE INGENIERIA MECATRÓNICA
CURSO:
Proyecto Final de Graduación

de Costa Rica

NOMBRE | FIRMA | FECHA | ACABADO GENERAL: N/A | DESIGNACIÓN Cremallera - Herramienta

DIBUJ. | J.MURILLO | | 10/29/2024
VERIF. | J.C.BRENES | | 10/29/2024
APROB. | J.C.BRENES | | 10/29/2024
FABR.
SISTEMA: | | | TOLERANCIAS: | TOLERANCIA EN: | | ESCALA: | FORMATO PROYECTO:

E

F

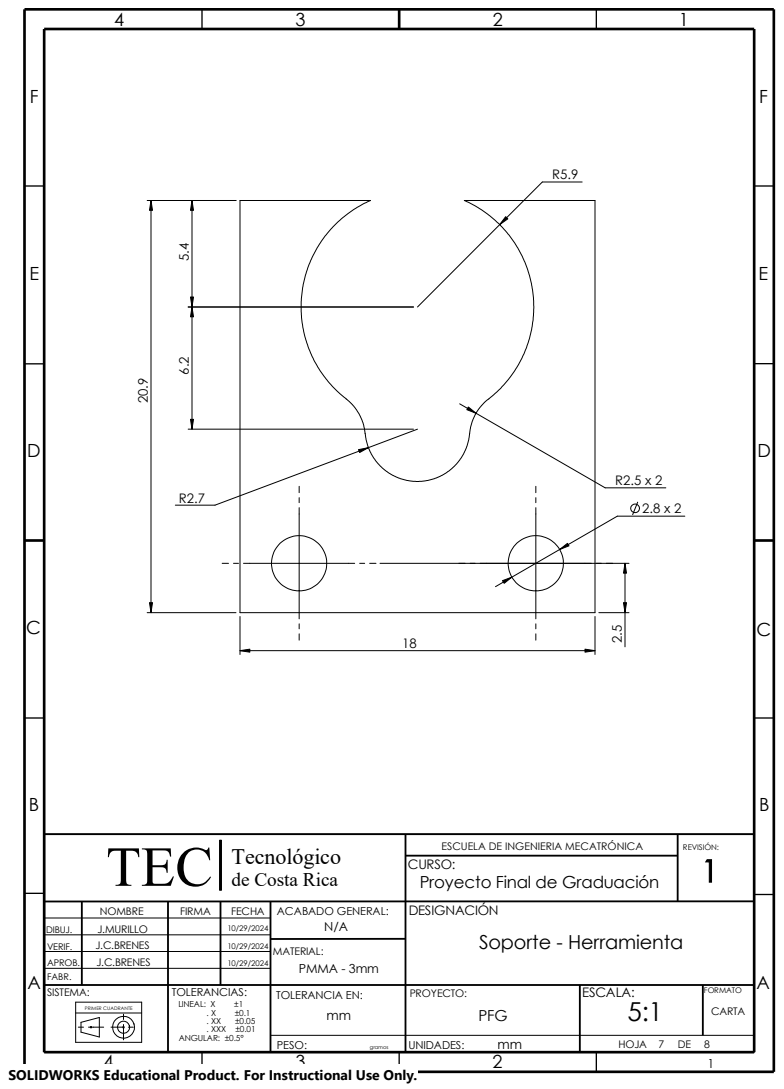
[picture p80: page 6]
Tecnológico TEC; PMMA - 3mm; REVISIÓN:; MATERIAL:

ESCUELA DE INGENIERIA MECATRÓNICA
CURSO:
Proyecto Final de Graduación

de Costa Rica

NOMBRE | FIRMA | FECHA | ACABADO GENERAL: N/A | DESIGNACIÓN Soporte - Herramienta

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

E

F

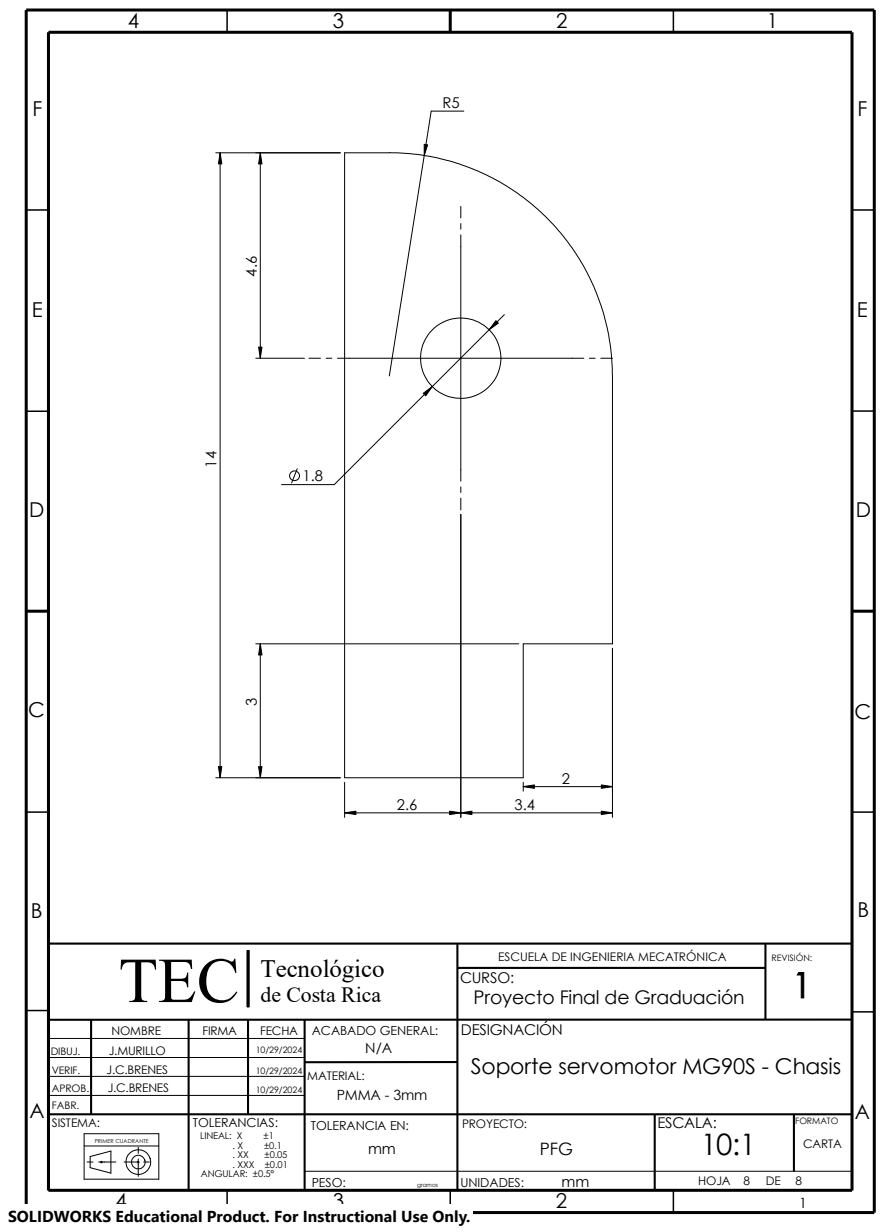
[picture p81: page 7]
Tecnológico TEC; PMMA - 3mm; REVISIÓN:; MATERIAL:

ESCUELA DE INGENIERIA MECATRÓNICA
CURSO:
Proyecto Final de Graduación

de Costa Rica

NOMBRE | FIRMA | FECHA | ACABADO GENERAL: N/A | DESIGNACIÓN Soporte servomotor MG90S - Chasis

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

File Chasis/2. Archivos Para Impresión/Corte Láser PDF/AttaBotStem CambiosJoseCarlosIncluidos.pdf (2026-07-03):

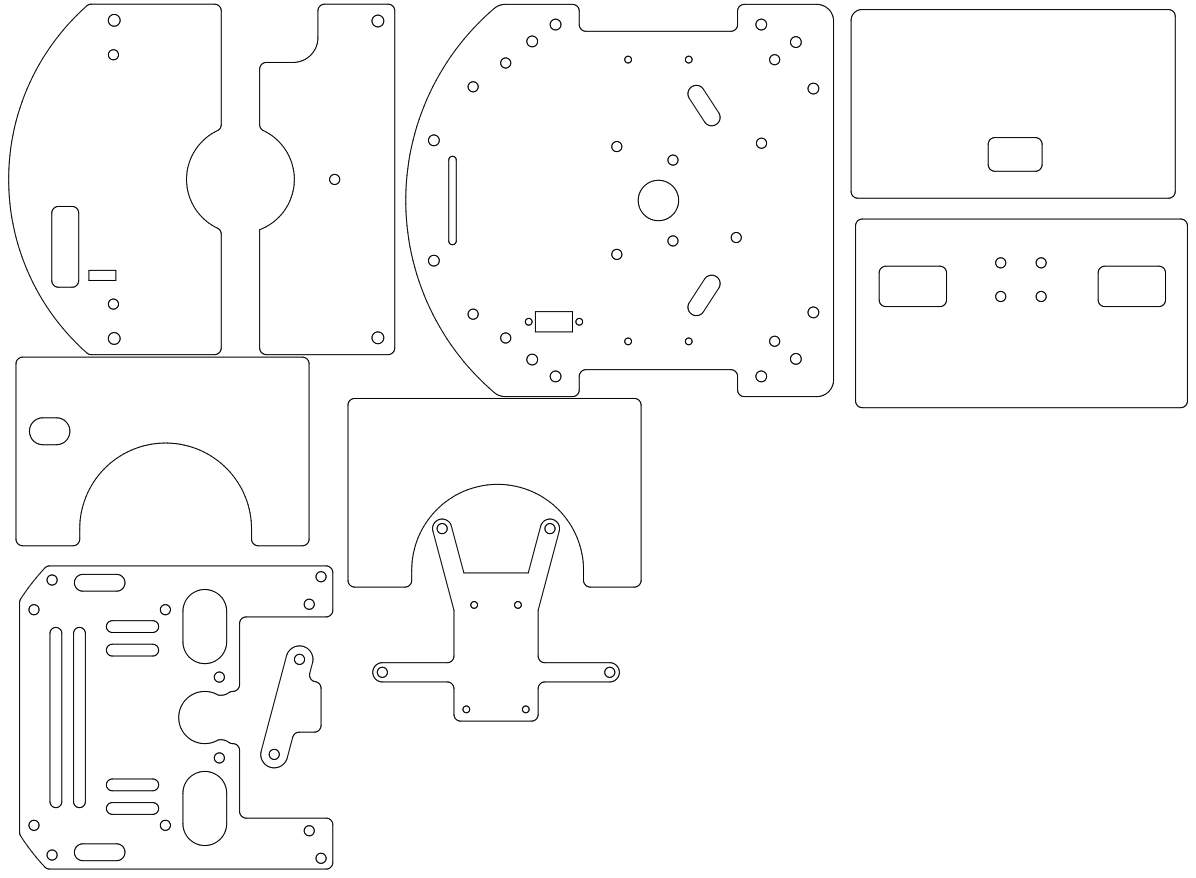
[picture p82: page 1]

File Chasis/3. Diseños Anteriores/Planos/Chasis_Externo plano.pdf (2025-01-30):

B

A

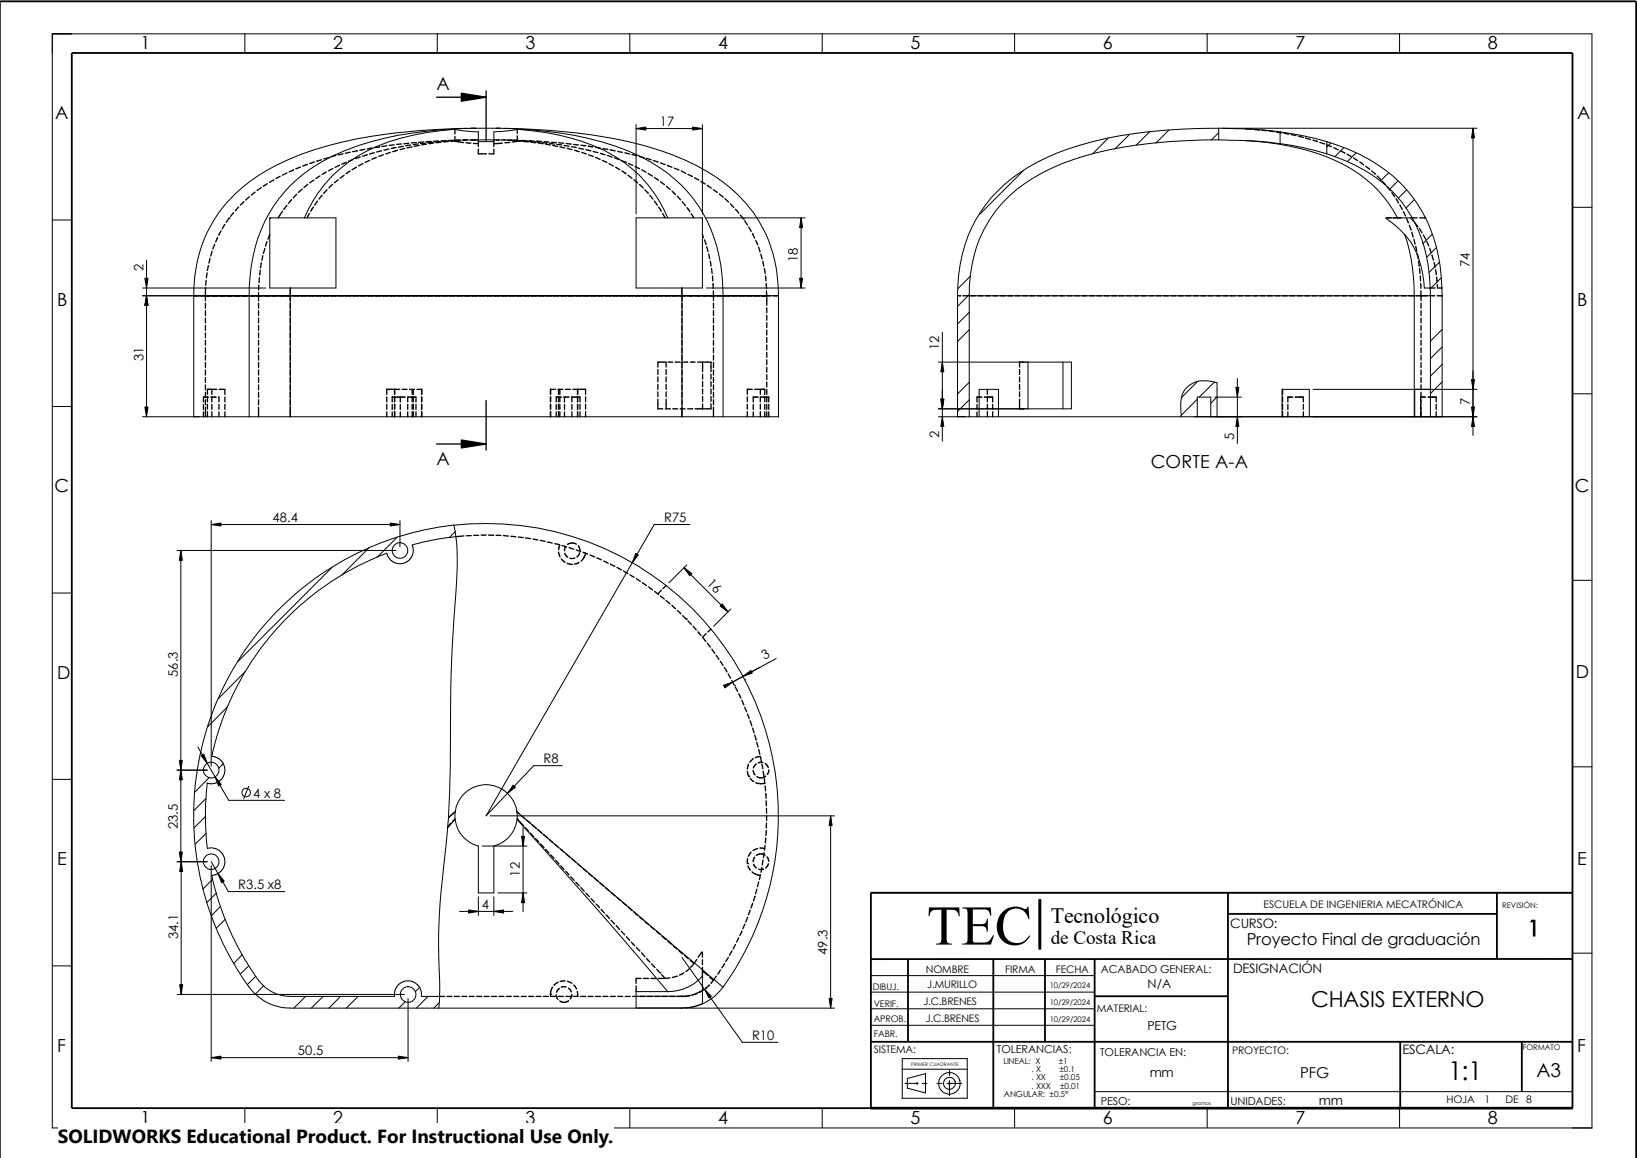
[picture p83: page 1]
Tecnológico TEC; PRIMER CUADRANTE; CURSO:; MATERIAL:; REVISIÓN:; PETG; HOJA; CORTE A-A

ESCUELA DE INGENIERIA MECATRÓNICA
Proyecto Final de graduación

de Costa Rica

NOMBRE | FIRMA | FECHA | ACABADO GENERAL: N/A | DESIGNACIÓN CHASIS EXTERNO

DIBUJ. | J.MURILLO | | 10/29/2024
VERIF. | J.C.BRENES | | 10/29/2024
APROB. | J.C.BRENES | | 10/29/2024
FABR.
SISTEMA: | | | LINEAL: X ±1 . X ±0.1 . XX ±0.05 . XXX ±0.01 ANGULAR: ±0.5° | TOLERANCIA EN: TOLERANCIAS: mm | PROYECTO: PFG | ESCALA: 1:1 | FORMATO A3

PESO: gramos | UNIDADES: mm

SOLIDWORKS Educational Product. For Instructional Use Only.

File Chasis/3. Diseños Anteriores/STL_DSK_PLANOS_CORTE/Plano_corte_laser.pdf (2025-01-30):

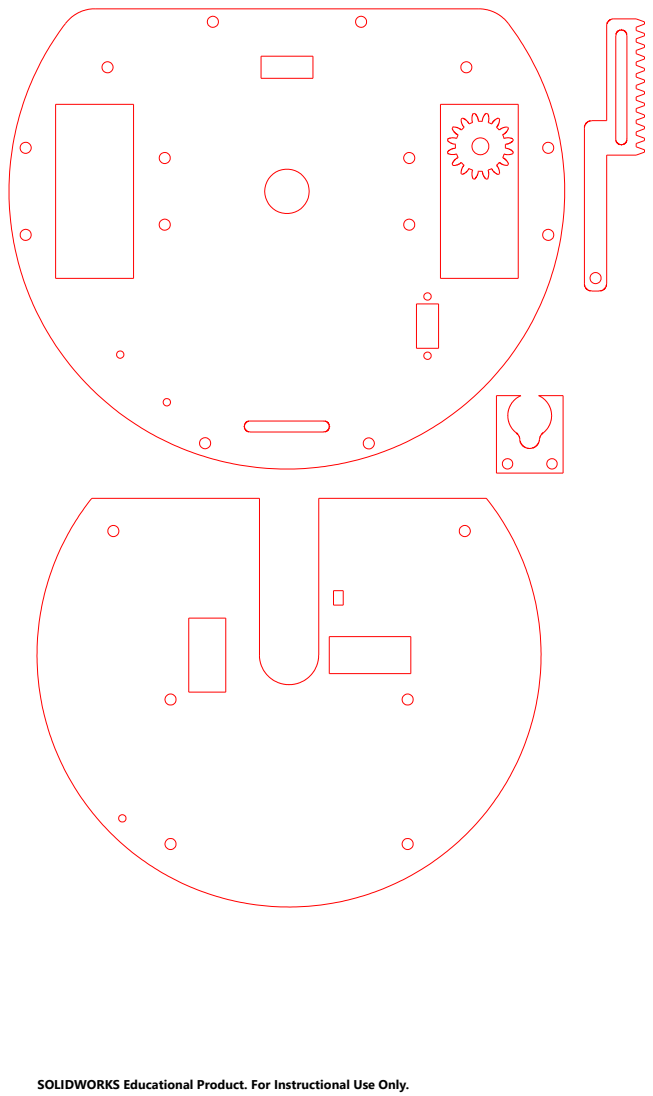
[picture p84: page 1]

SOLIDWORKS Educational Product. For Instructional Use Only.

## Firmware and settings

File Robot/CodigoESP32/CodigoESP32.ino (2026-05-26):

#include <ESP32Servo.h>
#include <ArduinoBLE.h>
#include <string>
using namespace std;

// Robot constants
const int samplingTime = 25; // units: miliseconds
const float rightPulsesPerRev = 834; // number of pulses from a single encoder output, for the right motor
const float leftPulsesPerRev = 834; // number of pulses from a single encoder output, for the left motor
const float wheelRadius = 22; // Wheel circumference = 139.5mm
const float distanceWheelToWheel = 120; // actualizado a chasís v2.4 
const float distanceCenterToWheel = distanceWheelToWheel / 2 ; // Turning radius of the robot, distance in mm between the center and one wheel

// Constants for PID control with samplingTime = 25ms
const float targetSpeed = 120.0; // Target speed for the robot in mm/s
const float kpSpeed = 2; // Proportional constant for speed control 0.75, 1.1
const float kiSpeed = 2; // Integral constant for speed control
const float kdSpeed = 0.0; // Derivative constant for speed control (set to zero for no derivative action)

// Constants for PID control implementation
const int minIntegralErrorSpeed = -255; // Minimum value for integral error to avoid windup
const int maxIntegralErrorSpeed = 255; // Maximum value for integral error to avoid windup

const int upperDutyCycleLimitSpeed = 200; // Maximum allowed PWM value for speed control
const int lowerDutyCycleLimitSpeed = 60; // Minimum allowed PWM value for speed control

// Constants for RGB LED configuration
const int duracionParpadeoLed = 500;
const int duracionIndicadorRecibeProgra = 100;//2000;

// Constants for Bluetooth connection
const int esperaBT = 500;
unsigned long tiempoPasadaLecturaBT = 0;

// Constante para determinar cuánto tiempo esperar a la hora de desactivar/activar el lápiz
const int esperaMovimientoServo = 100;

// Constante para evasión de obstáculos
const int distRetrocesoObstaculo = 50;

// Constante para tener siempre activos (o no) los sensores inferiores (trackers)
const bool trackersSiempreActivos = false;

// Error accumulation for speed PID control
float sumErrorVelRight = 0; // Accumulated integral error for the right wheel
float prevErrorVelRight = 0; // Previous error value for the right wheel (used for derivative calculation)
float sumErrorVelLeft = 0; // Accumulated integral error for the left wheel
float prevErrorVelLeft = 0; // Previous error value for the left wheel (used for derivative calculation)

int distanceTraveled = 0; // Variable to track the total distance traveled by the robot
const float correctionFactorLines = 0.95; //0.92 


int prevPWMRight = 0;
int prevPWMLeft = 0;
bool prevReverse = 0;


// For speed sampling
unsigned long previousTime = 0;

// Variables to keep track of the encoder state
volatile long leftEncoderPos = 0; // Current position of the left encoder (in ticks)
long leftTicksForSpeed = 0; // Number of encoder ticks counted for left wheel speed calculation
long leftPrevTicks = 0; // Previous encoder tick count for the left wheel (used to calculate speed) 
volatile long rightEncoderPos = 0; // Current position of the right encoder (in ticks)
long rightTicksForSpeed = 0; // Number of encoder ticks counted for right wheel speed calculation
long rightPrevTicks = 0; // Previous encoder tick count for the right wheel (used to calculate speed)

// Variables to store the servo position
const int activateAngle = 87;  // Activated Tool
const int deactivateAngle = 118; // Deactivated Tool
int set = 0;

//Variables del servomotor 360 del set de herramientas
const int pinServo360 = 23;
const int velocidadPositiva = 115; // ###
const int velocidadNegativa = 70; // ###
const int velocidadNeutra = 90; // ###

// Create a Servo object to control the MG90S
Servo myServo;
Servo servoHerramientaSet;


// Define pin for the servo signal
const int servoPin = 26;

// Define the encoder pins
const int rightEncoderA = 27; // Pin for the right encoder's channel A
const int rightEncoderB = 33; // Pin for the right encoder's channel B

const int leftEncoderA = 32; // Pin for the left encoder's channel A
const int leftEncoderB = 35; // Pin for the left encoder's channel B

// Motor control pins
const int rightMotorM1 = 14;   // Direction control pin 1 for the right motor
const int rightMotorM2 = 12;   // Direction control pin 2 for the right motor


const int leftMotorM1 = 13;   // Direction control pin 1 for the left motor
const int leftMotorM2 = 15;   // Direction control pin 1 for the left motor

// Obstacle sensors setup
const int rightInfraredSensor = 4; // Pin for the right infrared obstacle sensor
const int leftInfraredSensor = 34;  // Pin for the left infrared obstacle sensor

// Tracker sensors setup
const int rightTrackerSensor = 36;  // Pin for the right tracker sensor
const int leftTrackerSensor = 39;   // Pin for the left tracker sensor

// LED RGB setup
const int pinLedRgbRojo = 5; 
const int pinLedRgbVerde = 18; 
const int pinLedRgbAzul = 19;
const int pinBateriaBaja = 21;

unsigned long tiempoDeEncendidoDeLed = 0; // Variable para llevar los tiempos de parpadeo/cambio en led RGB

int currentStep = 0; // Variable to keep track of the current step
unsigned long stepStartTime = 0; // Variable to track the start time of each step


//variables máquina de estados
enum posibles_Estados {ESPERA=0, LEE_MEMORIA, MOVERSE, GIRAR, DETENERSE, CICLO, OBSTACULOS, MOVIMIENTO_OBSTACULO, HERRAMIENTA, HERRAMIENTA_SET, IF, WHILE, NADA};
posibles_Estados estado = ESPERA;
bool giro_listo = false;
bool movimiento_listo = true; 
bool obstaculos_activo = false;
bool primer_ciclo = true;
bool retroceso_listo = false;
bool obstaculo_detectado=false;
bool paro_emergencia=false;



//variables para comunicación Bluetooth
string mensajeBLE="ATINIAV020GD030CI003RE010GI090CIFINATFIN";  
BLEService servicio("4fafc201-1fb5-459e-8fcc-c5c9c331914b");
BLEStringCharacteristic caracteristico("beb5483e-36e1-4688-b7f5-ea07361b26a8", BLERead | BLEWrite, 512);
//char nombreBLErobot= "AttaBotSTEM";

//apuntadores y variables para la lista de instrucciones
enum posibles_Instrucciones {inst_Avanzar=1, inst_Retroceder, inst_GiroIzquierdo, inst_GiroDerecho, 
inst_CicloInicia, inst_CicloFin, inst_ObstaculoInicia, inst_ObstaculoFin, inst_HerramientaInicia, inst_HerramientaFin, inst_FinalMsg,
inst_HerramientaSet, inst_IfInicia,inst_Else, inst_IfFinal, inst_WhileInicia, inst_WhileFinal};
short lista_instrucciones[100][2];
short inst_final = 0;
short inst_actual = 0;
short instruccion = 0;
short valor_instruccion = 0;
short inst_inicio_ciclo = 0;
short cantidad_ciclos = 0;

//Variables para las flags para los estados del LED RGB
bool flagBluetooth = 0;
bool flagEjecucion = 0;
bool flagObstaculo = 0;
bool flagParar = 0;
bool recibeProgra = 0;
bool flancoNegRecibeProgra = 0;
unsigned long recibePrograTiempo0 = 0;

//Variables de control del flujo de bifurcaciones
// banderas de control de bifurcaciones
bool ignorarHastaIFFIN = false;
bool ignorarHastaElse = false;
bool ignorarHastaWHILEFIN = false;
// registros de anidacion WHILE
short indicesWhile[5] = {};
short anidamientoWhile = 0;
short anidamientoWhileIgnorar=0;
// registros de anidacion IF
short anidamientoIF=0;
short anidamientoIFIgnorar=0;

// Funciones de control de flujo 
bool ejecutandoRamaIf[5] = {};
const short sensorIzquierdoSobreNegro = 0;
const short sensorIzquierdoSobreBlanco = 10;

const short sensorDerechoSobreNegro = 0;
const short sensorDerechoSobreBlanco = 1;

const short sensorNoImporta = 999; // Else sin condicion
// traker son los del suelo
const short mientras = 0;
const short mientrasNo = 100; 

// saqué los bool de lectura a globales

  bool lecturaInfrarrojoDerecho;
  bool lecturaInfrarrojoIzquierdo;
  bool lecturaSensorTrackerDerecho;
  bool lecturaSensorTrackerIzquierdo;

// Constantes del set de herramientas
const short garraAbrir = 101; 
const short garraCerrar = 1;
const short gruaSubir = 102;
const short gruaBajar = 2;

const short posicionHerramientaPositiva = 1; // Garra abierta, Grua arriba
const short posicionHerramientaNegativa = 2; // Garra cerrada, grua abajo
short posicionHerramienta = 0; // al prender el robot no se conoce la posicion de la herramienta. La primera ejecución se confía en el usuario, para la segunda ejecución ya se conoce la posicion

const short tiempoGarra = 700;//###;
const short tiempoGrua = 4000;//###;

short tiempoDeAccion=0;
short velocidad=velocidadNeutra; 

//******************************************************************************************************************
// Function that updates the position of the right wheel encoder.
//
// This function increments the encoder position counter for the right wheel each time it is called. The counter 
// reflects the accumulated encoder pulses, allowing for the calculation of distance or speed based on pulses.
//
//******************************************************************************************************************
void rightUpdateEncoder() {
  // Update encoder positions based on direction
  rightEncoderPos ++;

}

//******************************************************************************************************************
// Function that updates the position of the left wheel encoder.
//
// This function increments the encoder position counter for the left wheel each time it is called. The counter 
// reflects the accumulated encoder pulses, which can be used to determine distance or speed based on pulse count.
//
//******************************************************************************************************************
void leftUpdateEncoder() {
  // Update encoder positions based on direction
  leftEncoderPos ++;
}


void setup() {

  // Set the PWM properties (50 Hz is typical for servos)
  myServo.setPeriodHertz(50);    // Standard 50Hz servo
  myServo.attach(servoPin, 500, 2400);  // Attach the servo on the pin with min/max pulse widths

  // Set encoder pins as inputs
  pinMode(rightEncoderA, INPUT_PULLUP);
  pinMode(rightEncoderB, INPUT_PULLUP);

  pinMode(leftEncoderA, INPUT_PULLUP);
  pinMode(leftEncoderB, INPUT_PULLUP);

  pinMode(rightMotorM1, OUTPUT);
  pinMode(rightMotorM2, OUTPUT);

  pinMode(leftMotorM1, OUTPUT);
  pinMode(leftMotorM2, OUTPUT);

  //Obstacle sensors set up
  pinMode(rightInfraredSensor, INPUT);
  pinMode(leftInfraredSensor, INPUT);

  // Tracker sensors set up
  pinMode(rightTrackerSensor, INPUT_PULLDOWN);
  pinMode(leftTrackerSensor, INPUT_PULLDOWN);

  // LED RGB set up
  pinMode(pinLedRgbRojo, OUTPUT);
  pinMode(pinLedRgbAzul, OUTPUT);
  pinMode(pinLedRgbVerde, OUTPUT);

  // Setup servo360
  pinMode(pinServo360, OUTPUT);
  servoHerramientaSet.attach(pinServo360);
  servoHerramientaSet.write(velocidadNeutra);

  // Señal de batería baja set up
  pinMode(pinBateriaBaja, INPUT_PULLUP);

  // Attach interrupts to encoder pins
  attachInterrupt(digitalPinToInterrupt(rightEncoderA), rightUpdateEncoder, CHANGE);
  attachInterrupt(digitalPinToInterrupt(rightEncoderB), rightUpdateEncoder, CHANGE);

  attachInterrupt(digitalPinToInterrupt(leftEncoderA), leftUpdateEncoder, CHANGE);
  attachInterrupt(digitalPinToInterrupt(leftEncoderB), leftUpdateEncoder, CHANGE);

  Serial.begin(115200);
  //Inicialización comunicación bluetooth BLE
  if (!BLE.begin()) {
    Serial.println("starting BLE failed!");
    while (1);
  }
  BLE.setLocalName("AttaBotSTEM");
  BLE.setAdvertisedService(servicio);
  servicio.addCharacteristic(caracteristico);
  BLE.addService(servicio);
  BLE.advertise();

  tiempoDeEncendidoDeLed = millis();
}



void loop() {
 
  BLEDevice central = BLE.central();

  lecturaInfrarrojoDerecho=digitalRead(rightInfraredSensor);
  lecturaInfrarrojoIzquierdo=digitalRead(leftInfraredSensor);
  lecturaSensorTrackerDerecho=digitalRead(rightTrackerSensor);
  lecturaSensorTrackerIzquierdo=digitalRead(leftTrackerSensor);
  int flagBateriaBaja = digitalRead(pinBateriaBaja);


  //Máquina de estados principal
  switch (estado) {

    case ESPERA:  { 
      // Leer la conexión BLE periódicamente
      if (millis() >= tiempoPasadaLecturaBT + esperaBT) {
        leerBluetooth(central);
        tiempoPasadaLecturaBT = millis();
      }

      //Lógica de estado siguiente
      if (flancoNegRecibeProgra) {
          flagEjecucion = 1; 
          estado = LEE_MEMORIA;
          inst_actual = 0;
      } else if (paro_emergencia) { // si se recibe un comando de detener mientras está en ESPERA, se ignora
        flagParar = 0; 
        paro_emergencia = 0;
      }
      break;
    }

    case LEE_MEMORIA:  { 
      if ( inst_actual != inst_final ){ // avanza en memoria de instrucciones
        instruccion = lista_instrucciones[inst_actual][0];
        valor_instruccion = lista_instrucciones[inst_actual][1];
        inst_actual++;         

      } 
      
      //Lógica de estado siguiente
      if (inst_actual == inst_final) { 
        estado = ESPERA;
        inst_actual = 0;
        flagEjecucion = 0;

      } else if (ignorarHastaIFFIN || ignorarHastaElse || ignorarHastaWHILEFIN){ //se leen e ignoran segmentos de instrucciones hasta marcas de ramas
        //if
          if ((ignorarHastaIFFIN || ignorarHastaElse) && (instruccion == inst_IfInicia)){
            anidamientoIFIgnorar++; // debe ignorar un "fin" extra

          } else if ((ignorarHastaIFFIN || ignorarHastaElse) && (instruccion == inst_IfFinal)){            
            if (anidamientoIFIgnorar == anidamientoIF){ // se llegó al fin de una rama
              ignorarHastaIFFIN = false;
              ignorarHastaElse = false;
              estado = IF;
              } else {
                anidamientoIFIgnorar--;
              }

          } else if (ignorarHastaElse && (instruccion == inst_Else)){
            ignorarHastaElse = false; // se llegó al inicio de una nueva rama
            estado = IF;

          } else if (ignorarHastaWHILEFIN){ // Whiles
            if (instruccion == inst_WhileInicia){
              anidamientoWhileIgnorar++; // se debe ignorar un fin extra

            } else if (instruccion == inst_WhileFinal){
              if(anidamientoWhileIgnorar == anidamientoWhile){
                ignorarHastaWHILEFIN = false; //se llegó al fin del ciclo
              } else {
                anidamientoWhileIgnorar--;
              }
            }
          }  // estado se mantiene igual, se salta el resto de comparaciones y lee nueva instruccion   
      
      }else if (instruccion == inst_Avanzar) {
        rightEncoderPos = 0; 
        leftEncoderPos = 0;
        estado = MOVERSE;

      }else if (instruccion == inst_Retroceder) {
        estado = MOVERSE;
        valor_instruccion = valor_instruccion * -1;
        rightEncoderPos = 0; 
        leftEncoderPos = 0;

      }else if (instruccion == inst_GiroIzquierdo) {
        estado = GIRAR;
        valor_instruccion = valor_instruccion * -1;
        rightEncoderPos = 0;
        leftEncoderPos = 0;

      }else if (instruccion == inst_GiroDerecho) {
        estado = GIRAR;
        rightEncoderPos = 0;
        leftEncoderPos = 0;
      
      }else if (instruccion == inst_CicloInicia  ||  instruccion == inst_CicloFin) {
        estado = CICLO;

      }else if (instruccion == inst_ObstaculoInicia  ||  instruccion == inst_ObstaculoFin) {
        estado = OBSTACULOS;
      
      }else if (instruccion == inst_HerramientaInicia  ||  instruccion == inst_HerramientaFin) {
        estado = HERRAMIENTA;

      } else if (instruccion == inst_HerramientaSet) {
        estado = HERRAMIENTA_SET;

      } else if (instruccion == inst_IfInicia || instruccion == inst_Else || instruccion == inst_IfFinal){
        estado = IF;

      } else if (instruccion == inst_WhileInicia || instruccion == inst_WhileFinal){
        estado = WHILE;
      }

      break; 
    }
    
    case MOVERSE: {

      //Ejecuta el estado de avanzar o retroceder
      //(es el mismo pero con distancia negativa)
      movimiento_listo= advanceDesiredDistance(valor_instruccion*10);

      // Leer la conexión BLE periódicamente
      if (millis() >= tiempoPasadaLecturaBT + esperaBT) {
        leerBluetooth(central);
        tiempoPasadaLecturaBT = millis();
      }

      //Lógica estado siguiente
      if (paro_emergencia) { 
        estado = DETENERSE;

      } else if ( movimiento_listo ) {
        estado = DETENERSE;
        
      } else if ((trackersSiempreActivos || obstaculos_activo) && (lecturaSensorTrackerDerecho||lecturaSensorTrackerIzquierdo)) {
        obstaculo_detectado=true;
        flagObstaculo = 1;
        estado=DETENERSE;

      } else if (obstaculos_activo) {
        if (!lecturaInfrarrojoDerecho||!lecturaInfrarrojoIzquierdo){
          obstaculo_detectado=true;
          flagObstaculo = 1;
          estado=DETENERSE;
        }
      }
      break;
    }

    case GIRAR: {

      //Ejecuta el estado de girar derecha o izquierda
      //(es el mismo pero con ángulo negativo)

      //giro
      movimiento_listo= turnDesiredAngle(valor_instruccion);

      // Leer la conexión BLE periódicamente
      if (millis() >= tiempoPasadaLecturaBT + esperaBT) {
        leerBluetooth(central);
        tiempoPasadaLecturaBT = millis();
      }

      //Lógica estado siguiente
      if (paro_emergencia) {
        estado = DETENERSE;

      }else if ( movimiento_listo ) {
        //movimiento_listo = false;
        estado = DETENERSE;

      } else if ((trackersSiempreActivos || obstaculos_activo) && (lecturaSensorTrackerDerecho||lecturaSensorTrackerIzquierdo)) {
        obstaculo_detectado=true;
        flagObstaculo = 1;
        estado=DETENERSE;

      } else if (obstaculos_activo) {
        if (!lecturaInfrarrojoDerecho||!lecturaInfrarrojoIzquierdo){
          obstaculo_detectado=true;
          flagObstaculo = 1;
          estado=DETENERSE;
        }
      }
      
      break;
    }

    case DETENERSE: {
      
      if (paro_emergencia || obstaculo_detectado) { //en caso de apretar STOP o detectar obstaculo
        flagEjecucion = 0;
        configureHBridge(false, 3, 0, 0); //Detiene el robot 
      } // Ojo que la funcion avanzar y girar ya detiene el robot al final
        //configureHBridgeTurn(false, 3, 0, 0);
      delay(500);
      flagParar = 0;
            
      //Lógica estado siguiente
      if (paro_emergencia){
        paro_emergencia=false;
        estado = ESPERA;     
      } else if (obstaculo_detectado){
        // Se reinician los valores de posición para que no tome en cuenta el movimiento recién interrumpido
        rightEncoderPos = 0; 
        leftEncoderPos = 0;
        estado = MOVIMIENTO_OBSTACULO;
      } else {
        estado = LEE_MEMORIA;
      }
      break;
    }

    case CICLO: {

      if ( instruccion == inst_CicloInicia  &&  primer_ciclo ){ //inicio ciclo, primera vez
        cantidad_ciclos = valor_instruccion;  //guarda cantidad de ciclos, primero 
        primer_ciclo = false;
        inst_inicio_ciclo = inst_actual-1;  //almacena apuntador a inicio de ciclo
        cantidad_ciclos--; //resta el primer ciclo que se va a ejecutar

      }else if ( instruccion == inst_CicloInicia  &&  !primer_ciclo ) { //inicio de ciclo, resto de veces
        cantidad_ciclos--;  //resta 1 a la cantidad de ciclos

      }else if ( instruccion == inst_CicloFin  &&  cantidad_ciclos != 0 ) { //final de ciclo, ciclos pendientes
        inst_actual = inst_inicio_ciclo; //devuelve el apuntador al inicio del ciclo

      }else if ( instruccion == inst_CicloFin  &&  cantidad_ciclos == 0 ) { //final de ciclo, última vez
        primer_ciclo = true; //reset de variable
      }


      //Lógica estado siguiente
      estado = LEE_MEMORIA;
      break;
    }

    case OBSTACULOS: {

      //*Activa la bandera de si detectar obstáculos y luego la desactiva
      if ( instruccion == inst_ObstaculoInicia ){
        obstaculos_activo = true;
      }else if ( instruccion == inst_ObstaculoFin ) {
        obstaculos_activo = false;
      }

      //Lógica estado siguiente
      estado = LEE_MEMORIA;
      break;
    }

    case MOVIMIENTO_OBSTACULO: {
      // *Genera el movimiento despues que un obstaculo se detectó, el cual corresponde a un retroceso
      retroceso_listo=advanceDesiredDistance(-1* distRetrocesoObstaculo);
      obstaculo_detectado=false;
      flagObstaculo = 0;
      
      // Lógica estado siguiente
      if (retroceso_listo) {
        estado = ESPERA;
      } 
      break;
    }

    case HERRAMIENTA: {

      //*Activa la bandera de si detectar obstáculos y luego la desactiva
      if ( instruccion == inst_HerramientaInicia ){
        controlServo(true);
      }else if ( instruccion == inst_HerramientaFin ) {
        controlServo(false);
      }

      delay(esperaMovimientoServo); // para que el servo tenga tiempo de moverse antes de que el robot avance a la siguiente instrucción

      //Lógica estado siguiente
      estado = LEE_MEMORIA;
      break;
    }

    case NADA: {
      break;
    }

    case IF: {
      verSernsores();
      bifurcacionIF();
      estado = LEE_MEMORIA;
      break;
    }

    case WHILE: {
      // Leer la conexión BLE periódicamente por si se requiere salir de un loop infinito
      if (millis() >= tiempoPasadaLecturaBT + esperaBT) {
        leerBluetooth(central);
        tiempoPasadaLecturaBT = millis();
      }

      verSernsores();
      bifurcacionWHILE();
      estado = LEE_MEMORIA;
      break;
    }

    case HERRAMIENTA_SET: {
      accionarHerramientaSet();
      estado = LEE_MEMORIA;
      break;
    }


  }

  flancoNegRecibeProgra = 0;
  // Reseteo de la señal de recibeProgra
  if (recibeProgra && millis() > recibePrograTiempo0 + duracionIndicadorRecibeProgra) {
    recibePrograTiempo0 = millis();
    recibeProgra = 0;
    flancoNegRecibeProgra = 1;
  }

  // Se asigna el color del LED RGB
  ConfigurarEstadoLedRgb(flagBateriaBaja, flagBluetooth, flagEjecucion, flagObstaculo, recibeProgra, flagParar);

  delay(5);
}
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

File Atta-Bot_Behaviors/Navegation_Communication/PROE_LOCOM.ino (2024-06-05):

//Código de locomoción y comunicacion para el proyecto PROE
//Usado en la placa Feather M0 RFM95
//https://github.com/jcbrenes/PROE

#include <Wire.h> //Bilbioteca para la comunicacion I2C
#include "wiring_private.h" // Necesario para el I2C secundario y usar pinPeripheral() function
#include <SPI.h> //Biblioteca para la comunicacion por radio frecuencia
#include <RH_RF69.h> //Biblioteca para la comunicacion por radio frecuencia
#include <RHDatagram.h> // Biblioteca para la comunicación con direcciones

/************ Serial Setup ***************/
#define debug 0

#if debug == 1
#define serialPrint(x) Serial.print(x)
#define serialPrintln(x) Serial.println(x)
#else
#define serialPrint(x)
#define serialPrintln(x)
#endif

//Variables del enjambre para la comunicación a la base
const uint8_t cantidadRobots = 3; //Cantidad de robots en enjambre. No cuenta la base, solo los que hablan.
unsigned long idRobot = 2; //ID del robot, este se usa para ubicar al robot dentro de todo el ciclo de TDMA.

// Variables para el proceso de arranque y transformación de coordenadas
int distCoordenadas; //Distancia inicial de los robot 
bool datoCoordenadas = false; // Primer dato STM32 es la distancia entre robots
int matTransformation[int(cantidadRobots)]; // Arreglo utilizao para transformar las coordenadas de los robots.
int cantPaquetesDistanciaEnviados = 0; //Variable para contar la cantidad de paquetes que envia con la medición inicial
int cantPaquetesDistanciaPorEnviar = 5; // Cantidad de paquetes a enviar para la medición inicial.
int posicionXAvanzarCoordenada = 0; // Posicion X a la que va a avanzar el robot en la funcion avanzarCoordenada
int posicionYAvanzarCoordenada = 0; // Posicion Y a la qu va a avanzar el robot en la funcion avanzarCoordenada
int errorAvanzarCoordenada = 30; // Error que se permita de la posicion XY de la funcion avanzarCoordenada, debe ser minimo el ancho de los Atta

// Variables recibidas por los otros Atta-Bots
int16_t posXRecibido;
int16_t posYRecibido;
int16_t rotRecibido;
int8_t tipSensRecibido;
int16_t disRecibido;
int16_t anguloRecibido;

//constantes del robot empleado
const int tiempoMuestreo=100000; //unidades: micro segundos
const float pulsosPorRev=206.0; //cantidad de pulsos de una única salida
const int factorEncoder=2; //cantidad de salidas de encoders que se están detectando (pueden ser 2 o 4)
const float circunferenciaRueda=139.5;//Circunferencia de la rueda = 139.5mm 
const float pulsosPorMilimetro=((float)factorEncoder*pulsosPorRev)/circunferenciaRueda; 
const float distanciaCentroARueda=63.7;// Radio de giro del carro, es la distancia en mm entre el centro y una rueda. 
const float conversionMicroSaMin=1/(60 * 1000000);// factor de conversion microsegundo (unidades del tiempo muestreo) a minuto
const float conversionMicroSaSDiv=1000000;// factor de conversion microsegundo (unidades del tiempo muestreo) a segundo
const float tiempoMuestreoS= (float)tiempoMuestreo/conversionMicroSaSDiv;

//constantes para control PID movimiento lineal para tiempoMuestreo=100000 us
const float velRequerida=120.0; //unidades mm/s
const float KpVel=0.4; //constante control proporcional
const float KiVel=0.65; //constante control integral
const float KdVel=0.0; //constante control derivativo

//constantes para control PID de giro 
const float KpGiro=3.0; //constante control proporcional
const float KiGiro=1.1;//constante control integral
const float KdGiro=0.17; //constante control derivativo

//constantes para control PID de la pose del robot 
const float KpPose=1.0; //constante control proporcional
const float KdPose=0.0; //constante control derivativo
const float KiPose=0.0; //constante control derivativo
const float velBase=120.0; //unidades mm/s

//Constantes para la implementación del control PID real
const int errorMinIntegralVelocidad=-255;
const int errorMaxIntegralVelocidad=255;
const int errorMinIntegralGiro=-110;
const int errorMaxIntegralGiro=110;
const int limiteSuperiorCicloTrabajoVelocidad=200;
const int limiteInferiorCicloTrabajoVelocidad=-200;
int limiteSuperiorCicloTrabajoGiro=110;
int limiteInferiorCicloTrabajoGiro=-110;
const int limiteSuperiorCicloTrabajoGiroCalibracion=50;
const int limiteInferiorCicloTrabajoGiroCalibracion=-50;
const int cicloTrabajoMinimo= 20;
const int minCiclosEstacionario= 20;
const float correcionVelRuedas = 0.5;

//Configuración de pines de salida para conexión con el Puente H
const int PWMA = 12; //Control velocidad izquierdo
const int AIN1 = 10; //Dirección 1 rueda izquierda
const int AIN2 = 1; //Dirección 2 rueda izquierda
const int PWMB = 5;  //Control velocidad derecha
const int BIN1 = 9;  //Dirección 1 rueda derecha
const int BIN2 = 6;  //Dirección 2 rueda derecha

//Configuración de los pines para la conexión con los Encoders
const int ENC_DER_C1 =  A0; //Encoders rueda derecha
const int ENC_DER_C2 =  A1;
const int ENC_IZQ_C1 =  A2; //Encoders rueda izquierda
const int ENC_IZQ_C2 =  A3;

//Configuracion de los pines de interrupcion de Obstáculos
const int INT_OBSTACULO = A4;

//Almacenamiento de datos de obstáculos
const int longitudArregloObstaculos = 100;

//Constantes algoritmo exploración
const int unidadAvance= 1000; //medida en mm que avanza cada robot por movimiento
const int unidadRetroceso= -50; //medida en mm que retrocede el robot al encontrar un obstáculo
const unsigned long limiteRetroceso= 5000; //Máximo tiempo (ms) permitido para completar el retroceso, si no termina en ese tiempo asume que tiene un obstaculo atras
unsigned long tiempoRetroceso=0; //Almacena el momento en que se cambia a estado de retroceso para usar el limite de tiempo
const int limiteGiro= 5000; //Máximo tiempo permitido para completar el giro, permite que siga el movimiento si no se puede completar el giro por obstaculo o no se logra estado estacionario
unsigned long tiempoGiro=0; //Almacena el momento en que se cambia al estado de giro

//Constantes comunicación I2C con STM
const int dirSTM= 8; 
const int cantBytesMsg= 10; //cantidad de bytes que se solicitan al STM
//Definición para usar el segundo puerto I2C
TwoWire segundoI2C(&sercom1, 11, 13);

//Constantes bus I2C periféricos
#define dirEEPROM B01010000 //Direccion de la memoria EEPROM
#define dirMag 0x0D //I2C Address para el HMC5883
//Radios de conversión según data sheet del MPU6050
#define A_R 16384.0
#define G_R 131.0

//VARIABLES GLOBALES

//Variables para la máquina de estados principal
enum PosiblesEstados {AVANCE=0, RETROCEDA, GIRE_DERECHA, GIRE_IZQUIERDA, ESCOGER_DIRECCION, GIRO, CONTROL_POSE, NADA};
//char const *PosEstados[] = {"AVANCE", "RETROCEDA", "GIRE_DERECHA", "GIRE_IZQUIERDA","ESCOGER_DIRECCION","GIRO", "NADA"};
PosiblesEstados estado = AVANCE;

bool banderaParar = false; // Detiene todo avance del robot


//variable que almacena el tiempo del último ciclo de muestreo
unsigned long tiempoActual = 0;
unsigned long tiempoMaquinaEstados = 0;
unsigned long tiempoPollingPeri = 0;
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

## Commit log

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2024-08-28 refactor: safestate
    committing to save satete of current change beacuse of hardware upgrades being installed on the system
2024-09-16 refactor: UI fixes and updates
    Commit so the next stage of connecting via the commands can get started
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2024-12-03 feature: fixed button positioning
2025-01-30 Update del PFG de Jimena
    [Base_Chasis_V3.SLDPRT, Nivel_interno_V2.SLDPRT, Pieza_EngraneLift_2.SLDPRT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]
2025-02-19 Fix instr_actual no reset
    [AttaSTEM_Leisel_Jimena.ino]
2025-02-28 feat: refactor de la página principal de control, se agrega gesture detector para poder moverse entre el historial y la pantalla principal
2025-03-01 fix: arreglo a la pagina de inicio ya que en diferentes dispositivos se desacomodaba el logo
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2025-04-10 Iteración 2 de Rediseño Mecánico de Diego y Carlos
    [EngraneMod_v2.ipt, SoporteServo.ipt, Sujetador_De_Marcador_2Largo_FULL.ipt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]
2025-04-23 Rediseño chasis v3
    [PruebaIntegracion.0004.iam, PruebaIntegracion.iam, acople_engrane.0001.ipt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]
2025-05-08 Chasís v2.3
    Se ajustaron dimensiones para usar el acrílico azul transparente del taller de Diseño Industrial, el cual tiene un espesor ligeramente menor a 3 mm.
    También se hicieron cambios leves a posicionamiento de agujeros.
    [EngraneMod_v2.0004.ipt, EngraneMod_v2.ipt, PruebaIntegracion.0004.iam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]
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2025-05-15 Actualización para chasis v2.3 y arreglar bug LED estado Run
    [base_nivel2.0028.ipt, base_nivel2.0030.ipt, base_nivel2.ipt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]
2025-05-28 Arreglar bug LED en estado recibe programación
    Cuando se recibía una programación, no siempre el número de veces que parpadeaba el led en azul era la misma
2025-06-23 Gemelo digital de robot v2.3
    [PruebaIntegracion.0008.iam, PruebaIntegracion.0055.iam, PruebaIntegracion.iam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]
2025-06-23 Correccion gemelo digital
    [PruebaIntegracion.0055.iam, PruebaIntegracion.0061.iam, PruebaIntegracion.iam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]
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2025-07-22 Ajustes CAD y código ESP
    [EngraneMod_v2.0004.ipt, EngraneMod_v2.0006.ipt, EngraneMod_v2.ipt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]
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2025-08-14 Corrección constantes ESP32 y ensamble
    Se corrigieron algunas constantes del código Arduino para que los movimientos sean más exactos.
    Modificaciones leves al ensamble para que esté igual al manual de usuario.
    [PruebaIntegracion.0003.ipn, PruebaIntegracion.0021.ipn, PruebaIntegracion.0113.iam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]
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2025-08-27 Chasís v2.5
    Se hicieron cambios al chasís con la finalidad de reducir su altura.
    Se modificaron las siguientes piezas:
    - Base inferior: reposicionamiento de espaciadores con base superior y del switch
    - Base superior: se recortó a los lados para que pasen las llantas sin interferencia, se ajustó el tamaño de los agujeros para cables, se movieron los sensores infrarrojos frontales, se movió la posición del espaciador trasero para base inferior
    - Sujetador de cremallera: se redujo distancia para que la cremallera quede más cerca del engrane
    - Cremallera: Se redujo el ancho de la ranura para tornillos del sujetador de cremallera para mejorar ajuste.
    - Pendiente reajuste del engrane al s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
    [PruebaIntegracion.0155.iam, PruebaIntegracion.0160.iam, PruebaIntegracion.iam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]
2025-08-28 Actualización chasís v2.5 y planos de corte
    Se movió el interruptor ligeramente par asegurar una mejor integración.
    Se aumentó la altura de la cremallera.
    Se agregaron los planos de corte láser de este chasís
    [Diseño v2.5.dwg, PruebaIntegracion.0160.iam, PruebaIntegracion.0165.iam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]
2025-08-29 Actualización_prueba_carcasa_v1
    [Carcasa_llanta_posible.0001.ipt, Carcasa_llanta_posible.ipt, PruebaIntegracion.0165.iam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]
2025-09-03 Actualización chasís v2.5
    Las piezas estandarizadas utilizadas ahora se encuentran en esta carpeta, para facilitar la colaboración en distintas computadoras
    [ISO 4032 - M2 - ISO.ipt, ISO 4032 - M3 - ISO.ipt, ISO 4762 - M2 x 12ISO.ipt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]
2025-09-04 Carcasa modelo genérico
    [PruebaIntegracion.0174.iam, PruebaIntegracion.0182.iam, PruebaIntegracion.iam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]
2025-09-04 Nueva carcasa piezas
    [carcasa.0024.ipt, carcasa.ipt, carcasa_piezasRadio_3.0.0003.ipt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]
2025-09-04 Actualizacion piezas carcasa 3.0
    [Carcasa_llanta_posible.ipt, carcasa.0024.ipt, carcasa.0025.ipt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]
2025-09-08 Piezas carcasa 3.0 y actualización
    [carcasa.0025.ipt, carcasa.0026.ipt, carcasa.ipt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]
2025-09-09 Actualización base carcasa
    [PruebaIntegracion.0182.iam, PruebaIntegracion.0184.iam, PruebaIntegracion.iam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]
2025-09-09 Actualización_carcasa_3.0
    [Ensamble_Carcasa3.0.0001.iam, Ensamble_Carcasa3.0.iam, carcasa.0026.ipt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]
2025-09-09 Actualización_carcasa3.0
    [carcasa3.0.0002.ipt, carcasa3.0.0003.ipt, carcasa3.0.ipt]
2025-09-09 Actualización_final_carcasa3.0
    [Ensamble_Carcasa3.0.0001.iam, Ensamble_Carcasa3.0.0002.iam, Ensamble_Carcasa3.0.iam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]
2025-09-10 Actualización carcasa y base superior
    [PruebaIntegracion.0184.iam, PruebaIntegracion.0186.iam, PruebaIntegracion.iam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]
2025-09-10 Actualización de carcasa
    [PruebaIntegracion.0186.iam, PruebaIntegracion.0187.iam, PruebaIntegracion.iam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]
2025-09-23 Actualización del pinout del ESP
    También se actualiza el valor de PPR a uno más cercano al de los motores de Zeta. Se corrige que a la hora de calcular distancia lineal se usaba solo el encoder derecho y se agregó un factor de corrección de inercia para los giros.
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2025-10-15 Diseño_carcasa_rediseño4.0
    [Ensamble_Carcasa4.0.0001.iam, Ensamble_Carcasa4.0.0002.iam, Ensamble_Carcasa4.0.iam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]
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2025-10-22 Paquetes kts
    Añadiendo paquetes kts para ver si soluciona el error al momento de hacer la apk
2025-10-30 Added motor calibration code and corrected wait time for BT read
    [CalibracionMotores.ino]
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2025-11-23 Agregar al ensamble el nuevo sistema de servo
    [Ensamble_completo.0017.iam, Ensamble_completo.0034.iam, Ensamble_completo.iam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]
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2026-02-26 Diseño V.4 Con Carcasa Exterior
    Se Diseña por completo la carcasa exterior con una combinación entre armadura en PLA y paredes de acrílico.
    [Acrilicos Superiores.0006.ipt, Acrilicos Superiores.ipt, Acrílicos superiores.0002.ipt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]
2026-02-26 Creación de Archivo pdf para corte de molde
    [AttaBot Stem Acrilics.0006.dwg, AttaBot Stem Acrilics.0008.dwg, AttaBot Stem Acrilics.dwg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]
2026-03-06 Simplified mode in cycle handling
    CommandService now tracks simplifiedMode and simplifiedCycleActive, adds logic to insert commands before an end-cycle marker, and provides initCycleSimplified to create paired init/end cycle commands. UI changes disable the cycle button in simplified mode, sync the mode state from BotControlPage to CommandService, reduce default cycle options, and prevent moving commands outside a cycle block in HistoryPage. Also remove redundant end-cycle injection in places relying on the new simplified cycle behavior.
2026-03-20 Pequeños cambios del Techo, Inicio de arreglo al guradabarros
    [Ensamble_completo.0096.iam, Ensamble_completo.0098.iam, Ensamble_completo.iam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]
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2026-03-27 Cambios en Guardabarros y orificios de sensores/powerBoost
    [Bumper Delantero.0008.ipt, Bumper Delantero.0009.ipt, Bumper Delantero.ipt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]
2026-04-11 STL y PDFS ultimos cambios, lesgou
    Falta una pequeña modificación a la prensa pilot
    [Acrilicos Superiores.0006.ipt, Acrilicos Superiores.0007.ipt, Acrilicos Superiores.ipt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]
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2026-04-16 NuevaPrensaPilot
    Se realizó una nueva presna para el pilot que utiliza spacers como guía lineales. Esto consecuentemente provocó cambios en los pisos de acrílico inferior y superior de los cuales se sujetan los mismo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
    [Acrilicos Superiores.0007.ipt, Acrilicos Superiores.0009.ipt, Acrilicos Superiores.ipt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]
2026-04-16 Archivos Corte Laser PDF Listos 100%
    Archivos de Impresion listos para ir donde Fabián bien temprano
    [PrensaPilotInventorVersion.stl]
2026-04-25 feat: Add landscape split mode switch and UI tweaks
    Integrate a ModeSwitch into LandingPage AppBar for landscape to toggle an alternate left/right pane split. Build left/right panes conditionally so toggling swaps BotControlPage, HistoryPage and SimulatorPage as needed.
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2026-05-16 Tornillería agregada faltante
    [Ensamble_completo.0112.iam, Ensamble_completo.0115.iam, Ensamble_completo.iam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]
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2026-05-20 Arreglo de los logos
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2026-05-22 May be: Arreglar Leer memoria
    [CodigoESP32.ino]
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2026-05-23 agregar reset a flags de ignorar en inst_final
    [CodigoESP32.ino]
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2026-05-23 Arreglas condiciones alto bajo (sensor alto en negro, bajo en blanco)
    [CodigoESP32.ino]
2026-05-23 Arreglo de While
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2026-05-25 Subir archivos Inventor del set de Herramientas
    [Acoplador.0002.ipt, Acoplador.ipt, AcopleMotor.0003.ipt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]
2026-05-25 Actualizar con el arreglo del else...if a elseif
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2026-06-08 feat: arreglo de merge
2026-06-08 feat: arreglo de pantallas

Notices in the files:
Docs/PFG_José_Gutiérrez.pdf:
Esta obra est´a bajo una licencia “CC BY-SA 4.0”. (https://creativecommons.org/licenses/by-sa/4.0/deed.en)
